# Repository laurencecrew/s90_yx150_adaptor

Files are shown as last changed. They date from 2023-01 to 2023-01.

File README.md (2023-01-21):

"# s90_yx150_adaptor" 

# Adaptor brackets for 196x Honda S90 frame to YX-150 or similar engine

Please see Solidworks files for full details of the assembly. I have not included drawings of the various mounting tubes except in the Solidworks files.

The engine adaptor bracket consists of
* 2 side plates from 3.2mm steel
* 3 frame mounting tubes (the original engine bolts run through these), and
* 2 engine mounting tubes (which run through the mounting points of the YX-150 engine).

Note that the left hand side plate has a bent offset section in it. The PDF drawing is a side view of the finished part and the DXF is the unfolded flat pattern. The right hand side plate is flat.

The frame mounting tubes shoud be brazed or welded to the side plates.

The engine mounting tubes each connect 2 shoulder bolts with an M6x1 internal thread. I used 4 x Honda brake master cylinder lever pivot bolts, part # 90114-MA5-671

The holes in the side plates should be counterbored to allow the bolt heads to be almost flush and fit inside the frame.

There is also an adaptor bracket to join the original foot peg assembly to the mounting holes in the bottom of the YX-150 casing. This assembly also includes turned bosses that should be brazed or welded to the flat section (see Solidworks files).

## Frame modifications

In my case the S90 frame was unmodified except for a small cutaway (half of a 12mm round) to clear one of the screw bosses on the motor. This corresponds with the 12mm diameter cutaway on the right hand side plate.

## Improvements

Shoulder bolts with countersunk heads might cause less stress than the counterbored ones, if any could be found. I think it is best to use shoulder bolts that go through the side plates straight into the motor mounting holes rather than just M6 countersunk screws for example.

A bracket could be welded on to hold the ignition coil in the space on top of the motor, under the frame. I made a clamp on bracket but I never made any drawings of it.

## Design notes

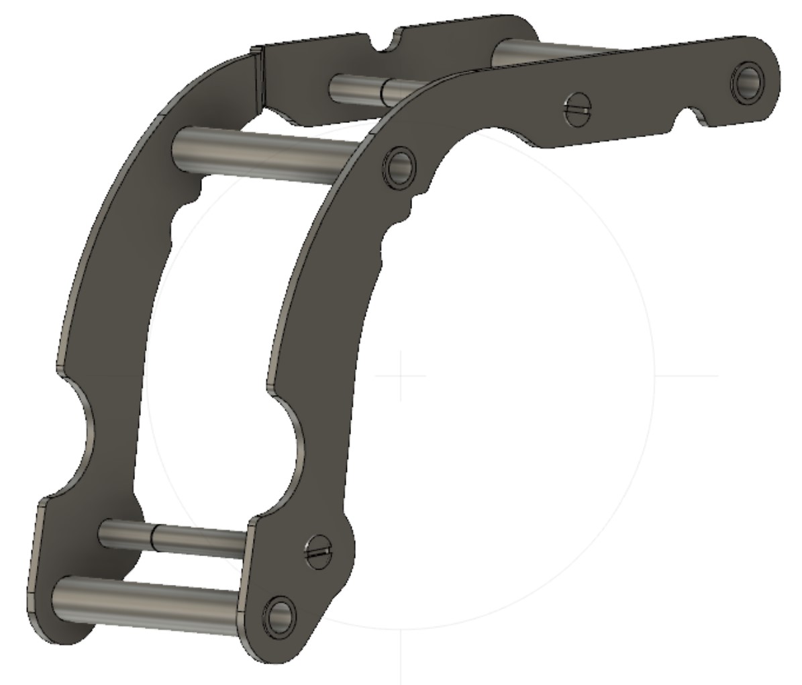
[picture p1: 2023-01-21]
engine_bracket_3D.jpg

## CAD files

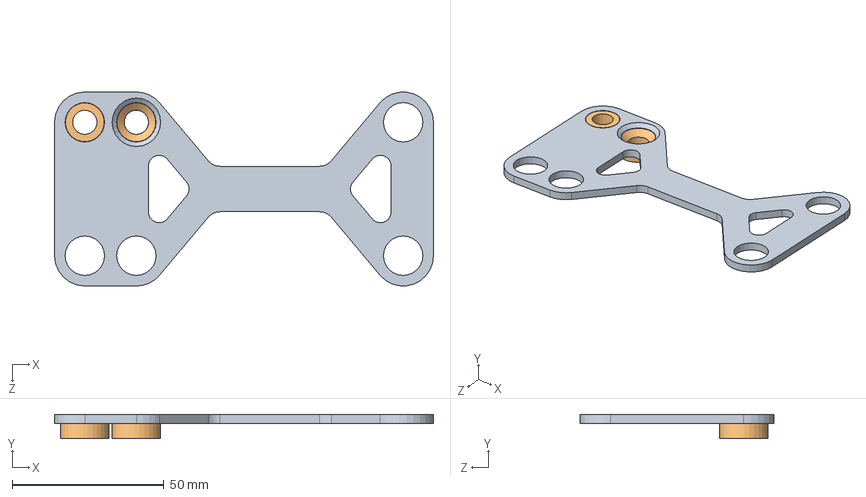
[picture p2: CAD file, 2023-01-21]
Solidworks/footpeg bracket.SLDASM
125.0 x 8.00 x 64.0 mm
Footpeg bracket
footpeg bracket boss x 2

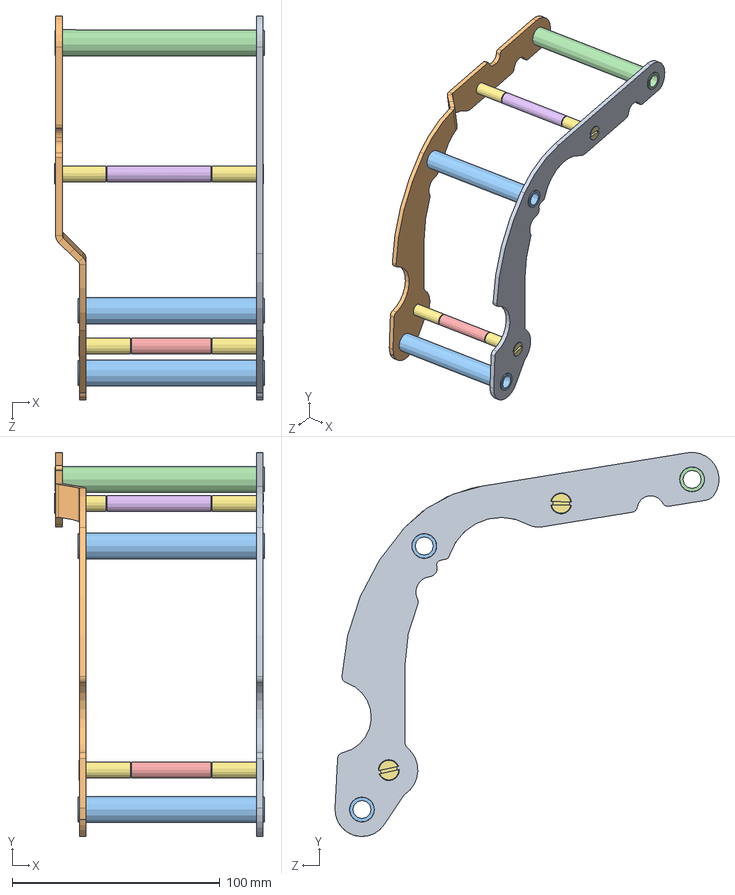
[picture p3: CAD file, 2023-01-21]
Solidworks/engine bracket.SLDASM
101.3 x 185.1 x 185.0 mm
engine bracket RHS
engine bracket LHS
frame mounting tube short x 2
frame mounting tube long
engine mounting tube short
engine mounting tube long
Shoulder_pin_screw_8x22xM6 x 4

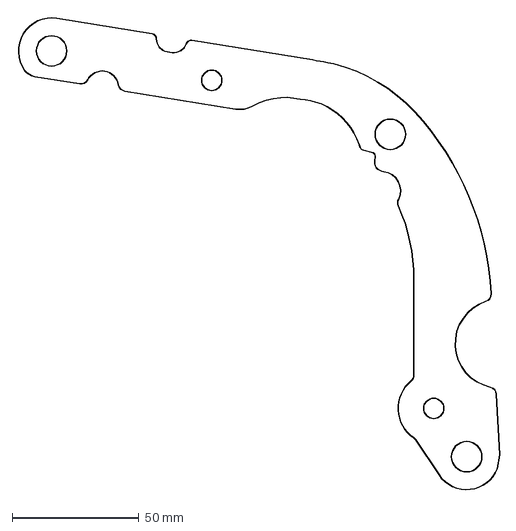
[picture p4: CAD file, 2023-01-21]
engine bracket LHS flat pattern.DXF
190.4 x 186.9 mm

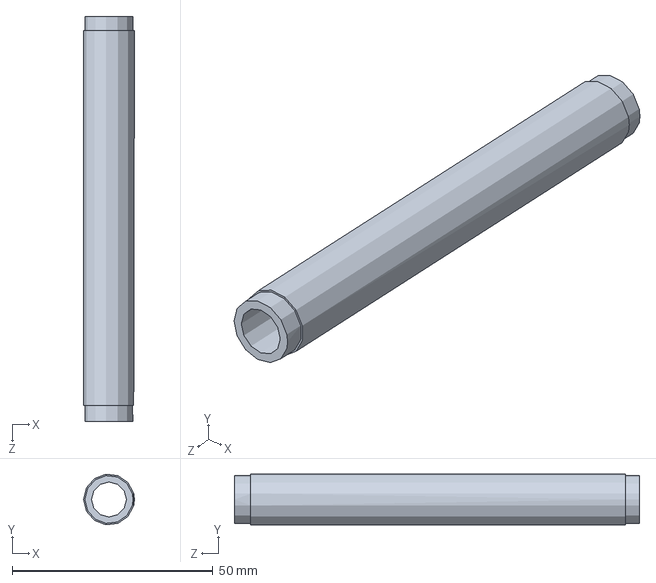
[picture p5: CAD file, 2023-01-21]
Solidworks/frame mounting tube long.SLDPRT
12.7 x 12.6 x 101.0 mm

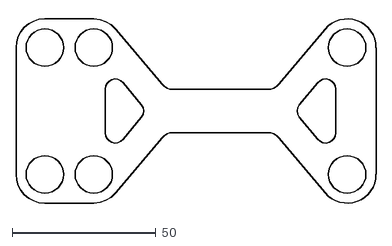
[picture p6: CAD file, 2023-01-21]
Footpeg bracket profile.DXF
125.0 x 65.7

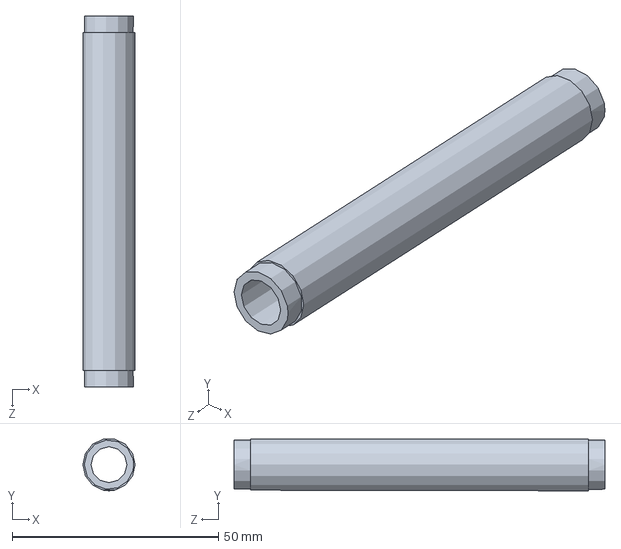
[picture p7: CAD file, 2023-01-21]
Solidworks/frame mounting tube short.SLDPRT
12.7 x 12.5 x 90.0 mm

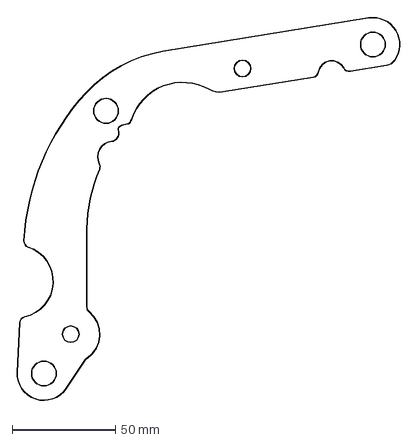
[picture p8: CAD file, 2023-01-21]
engine bracket RHS flat pattern.DXF
186.2 x 187.0 mm

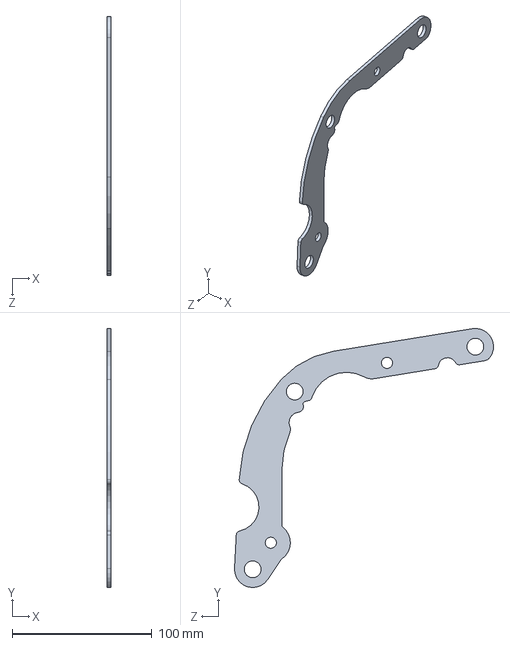
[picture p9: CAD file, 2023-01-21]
Solidworks/engine bracket basepart v2.SLDPRT
3.20 x 185.0 x 185.0 mm

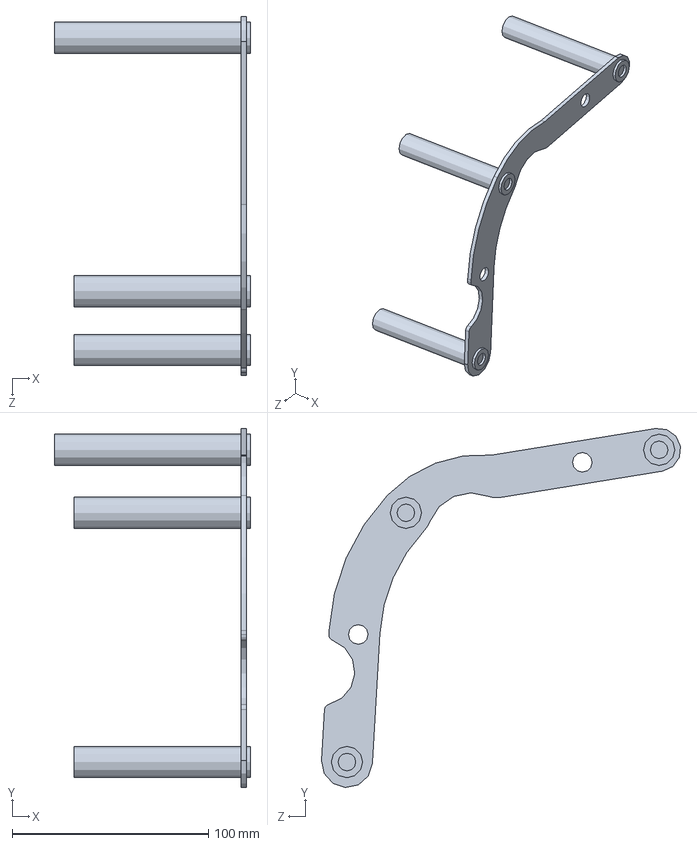
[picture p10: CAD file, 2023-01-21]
Solidworks/engine bracket v1.SLDPRT
100.0 x 182.9 x 182.9 mm

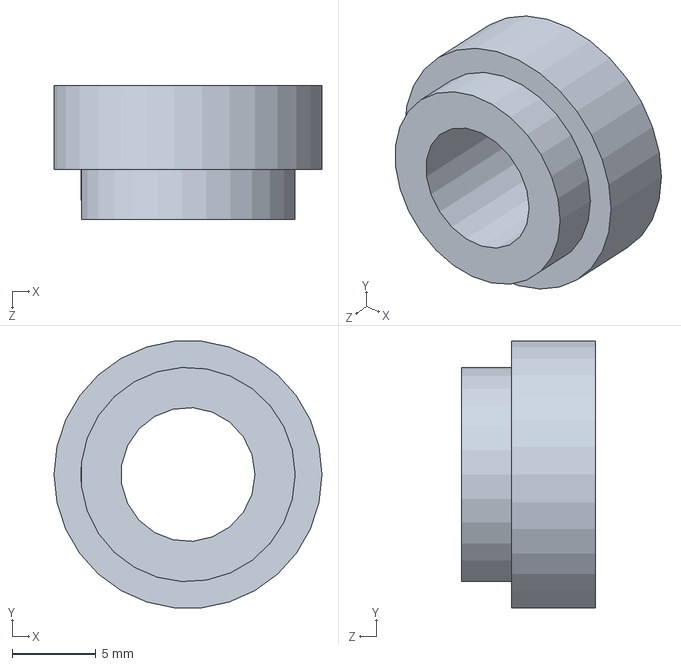
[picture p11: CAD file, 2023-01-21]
Solidworks/footpeg bracket boss.SLDPRT
16.0 x 15.9 x 8.00 mm

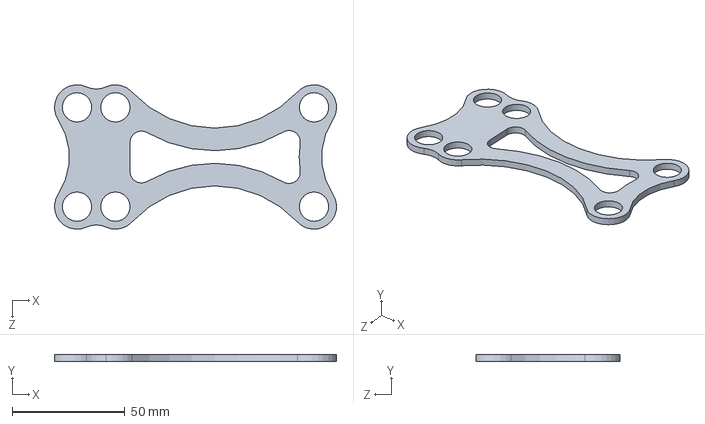
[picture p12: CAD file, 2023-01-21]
Solidworks/Footpeg bracket v1.SLDPRT
124.9 x 3.20 x 64.0 mm

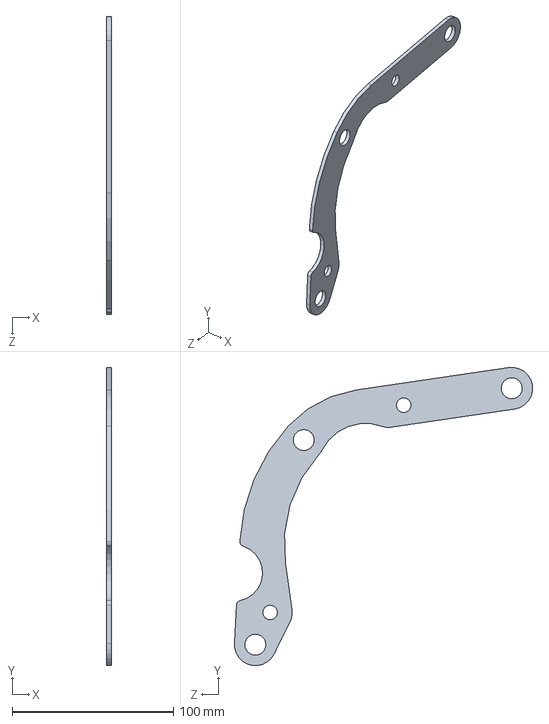
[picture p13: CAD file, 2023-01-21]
Solidworks/engine bracket basepart.SLDPRT
3.20 x 184.9 x 185.0 mm

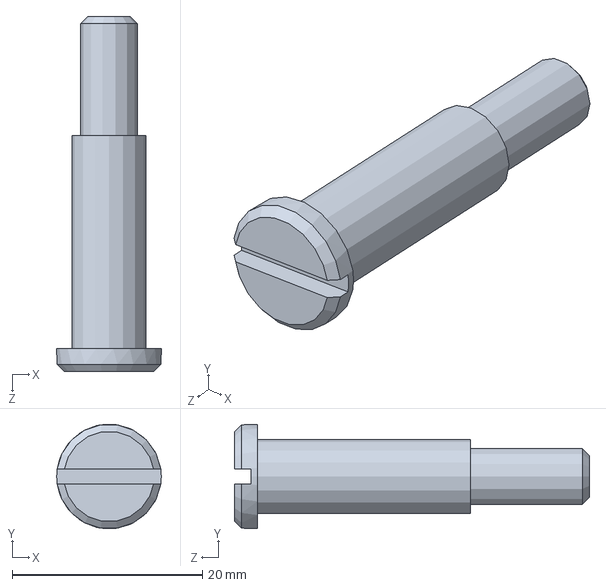
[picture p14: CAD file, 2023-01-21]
Solidworks/Shoulder_pin_screw_8x22xM6.SLDPRT
11.0 x 11.0 x 37.3 mm

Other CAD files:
Solidworks/engine bracket RHS.SLDPRT
Solidworks/engine bracket LHS.SLDPRT
Solidworks/engine mounting tube long.SLDPRT
Solidworks/engine mounting tube short.SLDPRT
Solidworks/Footpeg bracket profile.SLDDRW
Solidworks/Footpeg bracket.SLDPRT
Solidworks/engine bracket LHS.SLDDRW
Solidworks/engine bracket RHS.SLDDRW
Solidworks/engine bracket basepart.SLDDRW
Solidworks/engine bracket v1.SLDDRW
Solidworks/engine mounting tubes.SLDDRW
Solidworks/footpeg bracket boss.SLDDRW
Solidworks/frame mounting tubes.SLDDRW

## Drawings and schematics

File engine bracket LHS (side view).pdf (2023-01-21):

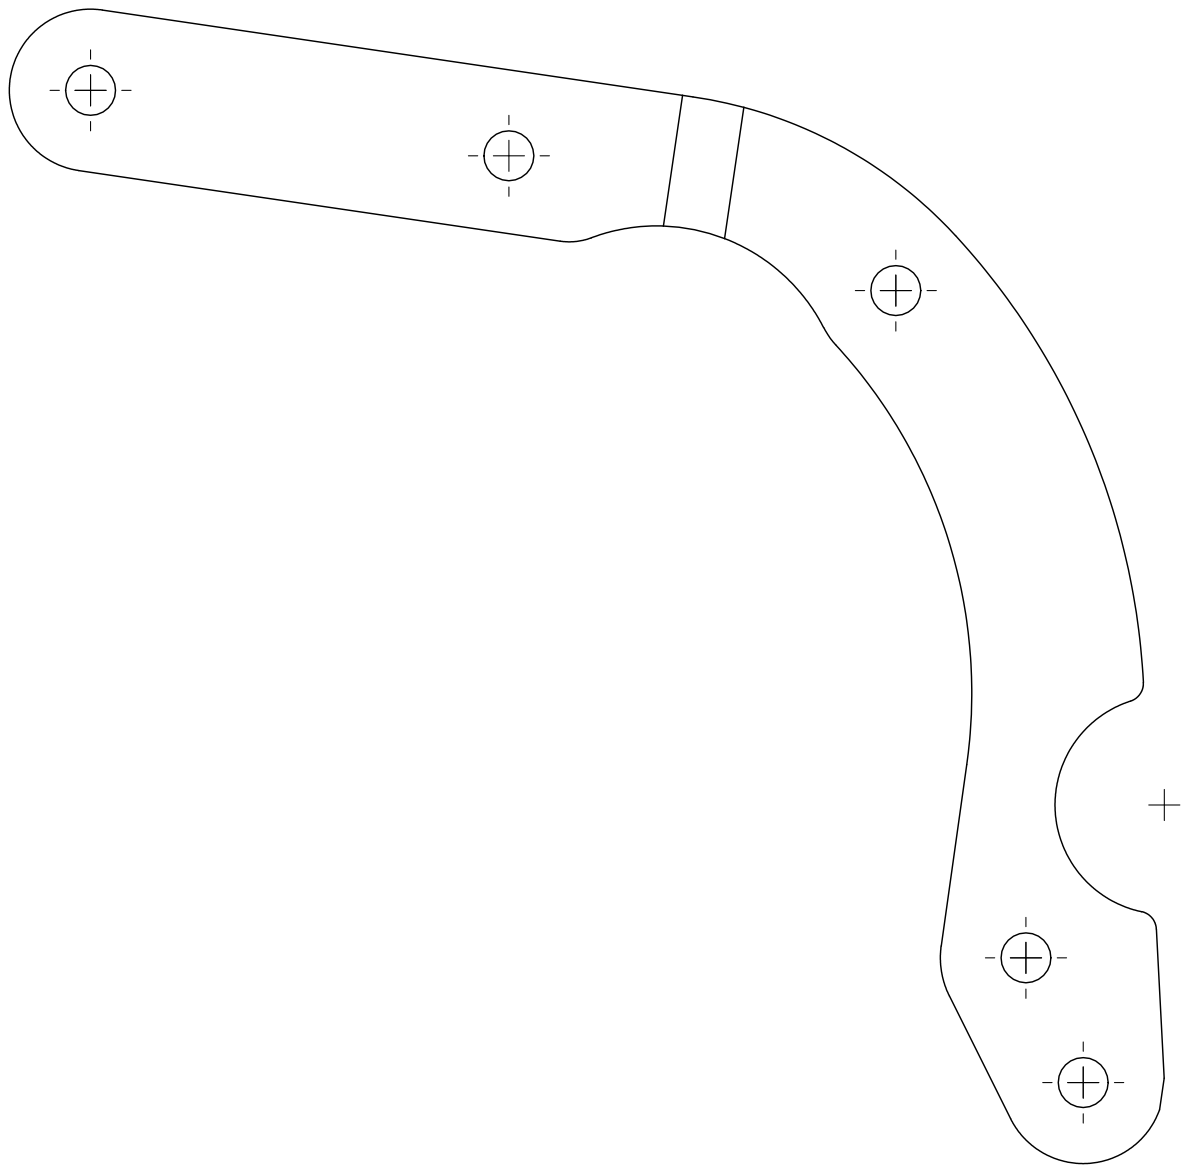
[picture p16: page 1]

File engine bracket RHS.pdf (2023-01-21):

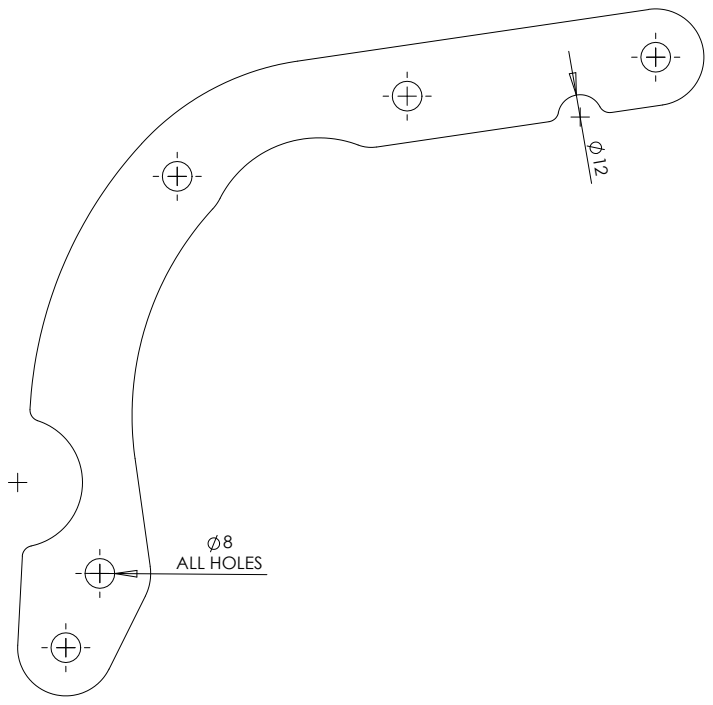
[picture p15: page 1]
ALL HOLES
